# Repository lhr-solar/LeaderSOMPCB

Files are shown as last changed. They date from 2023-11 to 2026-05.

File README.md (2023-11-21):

# LeaderSOM
Author: Pratyush Patra and Jacob Pustilnik (and Tianda Huang)

This board is the Leader System-On-Module (SOM), a multifunction board with an STM32 MCU that is adaptible to the applications of each subsystem. The hardware and software on this board are responsible
for the processing, communication, and data collection tasks required for the car's subsystems.

## BOM
[**Interactive BOM (Must download and open in browser)**](bom/ibom.html)

[**Mouser Cart**]

## Connectors
| # | Name | Type | Ideal Voltage | Notes |
| - | - | - | - | - |

## PCB

## Schematic

## Additional Notes

## Current Board Concerns(8.26.2023)

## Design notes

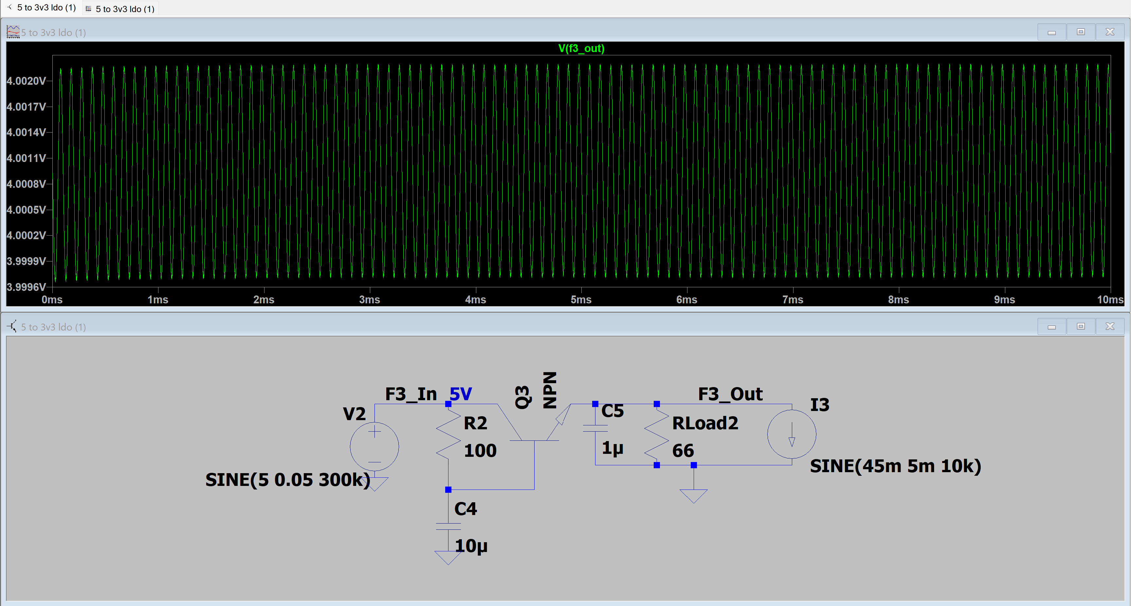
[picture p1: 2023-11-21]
PowerDistributionScreenshots/CapMultiplier.png

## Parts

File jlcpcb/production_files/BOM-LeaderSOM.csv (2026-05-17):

Comment | Designator | Footprint | LCSC | Quantity
0.1uF | C1,C11,C12,C19,C23,C24,C25,C26,C27,C28,C29,C30,C32,C35,C36,C37,C38,C39,C40,C41,C44,C5,C7,C8 | C_0603_1608Metric_Pad1.08x0.95mm_HandSolder | C14663 | 24
10k | R1,R12,R17,R22,R23,R29,R32,R33,R9 | R_0603_1608Metric_Pad0.98x0.95mm_HandSolder | C25804 | 9
10nF | C16 | C_0603_1608Metric_Pad1.08x0.95mm_HandSolder | C57112 | 1
10uF | C10,C13,C14,C20,C21,C22,C3,C42,C45 | C_0805_2012Metric_Pad1.18x1.45mm_HandSolder | C440198 | 9
120 | R10,R2 | R_0603_1608Metric_Pad0.98x0.95mm_HandSolder | C22787 | 2
16k | R15 | R_0603_1608Metric_Pad0.98x0.95mm_HandSolder | C137788 | 1
19k | R31 | R_0603_1608Metric_Pad0.98x0.95mm_HandSolder | C22893 | 1
1k | R19,R21,R28,R34,R35,R8 | R_0603_1608Metric_Pad0.98x0.95mm_HandSolder | C21190 | 6
1uF | C15,C18,C2,C43,C46,C9 | C_0603_1608Metric_Pad1.08x0.95mm_HandSolder | C15849 | 6
2.1k | R26 | R_0603_1608Metric_Pad0.98x0.95mm_HandSolder | C2960801 | 1
2.2k | R11,R3 | R_0603_1608Metric_Pad0.98x0.95mm_HandSolder | C4190 | 2
22.1k | R6 | R_0603_1608Metric_Pad0.98x0.95mm_HandSolder | C31850 | 1
24V | D4 | LED_0603_1608Metric_Pad1.05x0.95mm_HandSolder | C7371904 | 1
26p | C31,C33 | C_0603_1608Metric_Pad1.08x0.95mm_HandSolder | C92670 | 2
3.3nF | C17 | C_0603_1608Metric_Pad1.08x0.95mm_HandSolder | C107088 | 1
332 | R14 | R_0603_1608Metric_Pad0.98x0.95mm_HandSolder | C103549 | 1
3V3 | D21,D5 | LED_0603_1608Metric_Pad1.05x0.95mm_HandSolder | C7371904 | 2
4.3k | R18,R20 | R_0603_1608Metric_Pad0.98x0.95mm_HandSolder | C2907165 | 2
4.7uF | C34 | C_0805_2012Metric | C106218 | 1
4.7uF | C4,C6 | C_0805_2012Metric | C98192 | 2
402k | R27 | R_0603_1608Metric_Pad0.98x0.95mm_HandSolder | C2960796 | 1
45.3k | R24 | R_0603_1608Metric_Pad0.98x0.95mm_HandSolder | C2933224 | 1
47.5k | R7 | R_0603_1608Metric_Pad0.98x0.95mm_HandSolder | C25819 | 1
49.9 | R13 | R_0603_1608Metric_Pad0.98x0.95mm_HandSolder | C849792 | 1
5.1k | R4,R5 | R_0603_1608Metric_Pad0.98x0.95mm_HandSolder | C23186 | 2
590 | R25 | R_0603_1608Metric_Pad0.98x0.95mm_HandSolder | C23084 | 1
5V | D7 | LED_0603_1608Metric_Pad1.05x0.95mm_HandSolder | C7371904 | 1
74AHC1G32 | U8 | SOT-23-5 | C7470 | 1
8K | R30 | R_0603_1608Metric_Pad0.98x0.95mm_HandSolder | C2960681 | 1
8M | Y1 | Crystal_SMD_Abracon_ABM3-2Pin_5.0x3.2mm | C144380 | 1
BUCK | D20 | LED_0603_1608Metric_Pad1.05x0.95mm_HandSolder | C7371904 | 1
CDSOT23-T24CAN | U1,U3 | CDSOT23-T24CAN | C2959841 | 2
CP2102N-Axx-xQFN24 | U2 | CP2102N-A02-GQFN24 | C969151 | 1
D5V0P4UR6SO-7 | CR1,CR2,CR3 | D5V0P4UR6SO-7 | C531179 | 3
D_Schottky | D1,D18 | D_SOD-123 | C82544 | 2
D_TVS | D16 | D_SOD-323 | C207246 | 1
FerriteBead | FB1,FB2 | L_0603_1608Metric_Pad1.05x0.95mm_HandSolder | C14709 | 2
LED | CC_FLT1,IC_FLT1 | LED_0603_1608Metric_Pad1.05x0.95mm_HandSolder | C7371904 | 2
LM76202QPWPRQ1 | IC3 | LM76202QPWPRQ1 | C1849484 | 1
LT1963AEST-3.3#TRPBF | U4 | SOT-223-3_TabPin2 | C459918 | 1
MBR230S1F | D3 | D_SOD-123F | C151335 | 1
Micro_SD_Card_Det | J4 | microSD_HC_Hirose_DM3AT-SF-PEJM5 | C114218 | 1
PFLT | D6 | LED_0603_1608Metric_Pad1.05x0.95mm_HandSolder | C7371904 | 1
SD12_SOD323 | D17 | D_SOD-323 | C207246 | 1
SP0503BAHT | D2 | SOT-143 | C7074 | 1
STM32G473RETx | U7 | LQFP-64_10x10mm_P0.5mm | C730120 | 1
TCAN337DCNR | IC1,IC2 | TCAN337DCNR | C2671619 | 2
TPS2115ADRBR | U5 | SON65P300X300X100-9N | C140321 | 1
TPS5405DR | U6 | TPS5405DR | C488409 | 1
USB | D19 | LED_0603_1608Metric_Pad1.05x0.95mm_HandSolder | C7371904 | 1
USB_C_Receptacle_USB2.0_16P | J3 | USB_C_Receptacle_GCT_USB4105-xx-A_16P_TopMnt_Horizontal | C393939 | 1
WS2812B-2020 | D10,D11,D12,D13,D14,D15,D8,D9 | WS2812B-2020 | C965555 | 8
SWD | SWD1 | Molex_Nano-Fit_105309-xx04_1x04_P2.50mm_Vertical |  | 1
Reset | Reset1 | TL3365AF180QG |  | 1
100uH | L1 | L_Coilcraft_MSS1246-XXX |  | 1
SW_SPDT | SW1 | SW_CJS-1200TA |  | 1
52465-2470 | J1 | 524652470 |  | 1
52465-2470 | J2 | 524652470 |  | 1
TP_AddressableLED | TP1 | TestPoint_Pad_1.0x1.0mm |  | 1

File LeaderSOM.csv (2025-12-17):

Value | Qty | Mouser Part Number | DNP
0.1uF | 23 | MLASH168SB7104KTNA01
1uF | 6 | MLASU168SB5105KTNA01
10uF | 9 | GRM21BR61H106KE43K
4.7uF | 3 | 08055D475KAT4A
10nF | 1 | MSASH168SB5103KTNA01
3.3nF | 1 | 06035C332K4T2A
26p | 2 | 0603N270F500CT
100nF | 1 | MLASH168SB7104KTNA01
LED | 2 | 604-APTD2012LCGCK
D5V0P4UR6SO-7 | 3 | 621-D5V0P4UR6SO-7
D_Schottky | 1 | 1N5819HW-7-F
SP0503BAHT | 1 | 576-SP0503BAHTG
MBR230S1F | 1 | MP01EA06
24V | 1 | XL-1608UBC-06A
3V3 | 1 | XL-1608UBC-06A
PFLT | 1 | XL-1608UBC-06A
BUCK | 1 | XL-1608UBC-06A
WS2812B-2020 | 8 | WS2812-2020
D_TVS | 1 | 771-PESD15VL1BA-T/R
SD12_SOD323 | 1 | 771-PESD15VL1BA-T/R
TVS | 1 | MP01EA06
FerriteBead | 2 | 704-MFBW1V2012-121-R
TCAN337DCNR | 2 | 595-TCAN337DCNR
LM76202QPWPRQ1 | 1 | 595-LM76202QPWPRQ1
52465-2470 | 2 | 538-52465-2470
USB_C_Receptacle_USB2.0_16P | 1 | 640-USB4105-GF-A
Micro_SD_Card_Det | 1 | DM3AT-SF-PEJM5
100uH | 1 | MSS1246-104MLC
10k | 7 | CRCW060310K0FKEI
120 | 3 | CRCW0603120RFKEC
2.2k | 2 | CRCW06032K10FKEA
5.1k | 2 | CRCW06035K10FKEC
22.1k | 1 | CRCW060322K1FKEBC
47.5k | 1 | CRCW060347K5FKEAHP
1k | 1 | CRCW06031K00FKEI
49.9 | 1 | RT0603BRE0750RL
332 | 1 | CRCW0603332RFKEAHP
16k | 1 | CRCW060316K0FKEA
4.3k | 2 | CRCW06034K30FKTA
768 | 1 | CRCW0603768RFKEA
45.3k | 1 | CRCW060345K3FKEAHP
590 | 1 | CRCW0603590RFKEA
2.1k | 1 | CRCW06032K10FKEA
402k | 1 | CRCW0603402KFKEAC
10K | 1 | CRCW060310K0FKEI
8K | 1 | CRCW060310K0FKEI
19k | 1 | CRCW060320K0FKEA
Reset | 1 | 653-B3SL-1002P
SW_SPDT | 1 | CJS-1200TA
SWD | 1 | 105309-1104
CDSOT23-T24CAN | 2 | CDSOT23-T24CAN
CP2102N-Axx-xQFN24 | 1 | CP2102N-A02-GQFN24
LT1963AEST-3.3#TRPBF | 1 | LT1963AEST-3.3#TRPBF
TPS2115ADRBR | 1 | TPS2115ADRBR
TPS5405DR | 1 | TPS5405DR
STM32G473RETx | 1 | STM32G473RET6
74AHC1G32 | 1 | SN74AHC1G32TDBVRQ1
8M | 1 | ABM3-8.000MHZ-D2Y-T

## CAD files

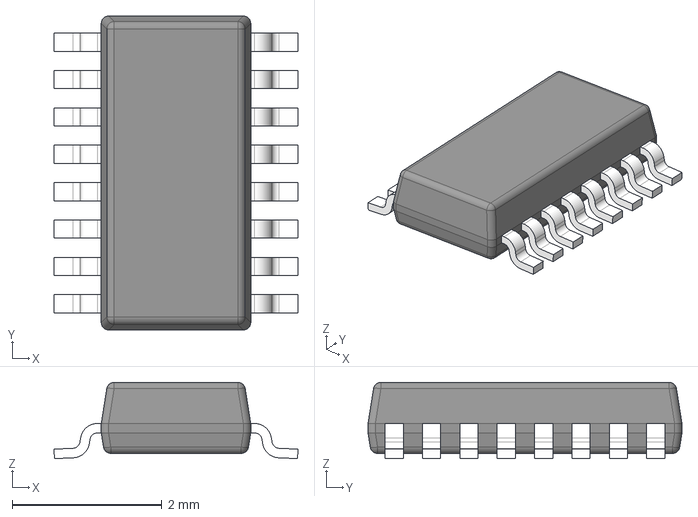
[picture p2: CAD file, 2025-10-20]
LSOM KiCad Libararies/SN74HCS595DYYR/DYY0016A.stp
3.26 x 4.20 x 1.02 mm
BODY-TSSOP
LEAD-TSSOP x 16

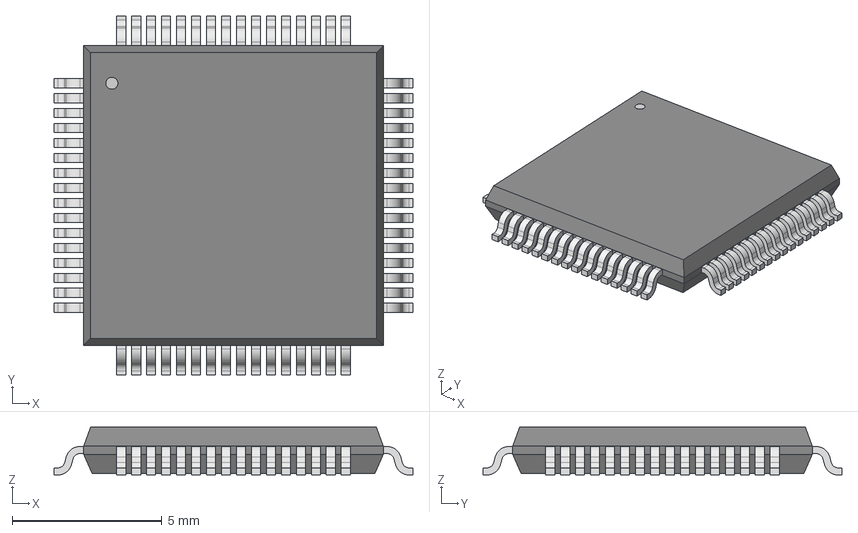
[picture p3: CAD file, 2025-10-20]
LSOM KiCad Libararies/STM32G473RET6/LQFP64-10x10mm.step
12.0 x 12.0 x 1.60 mm

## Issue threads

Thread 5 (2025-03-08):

Wrong Resistor Value for Power Protection

KadhirTheEngineer, 2025-03-08:
The 100k Pull up resistor for the UVLO pin on the Power Protection chip should be 10k resistor to get the right UVLO and OVLO values for the chip.

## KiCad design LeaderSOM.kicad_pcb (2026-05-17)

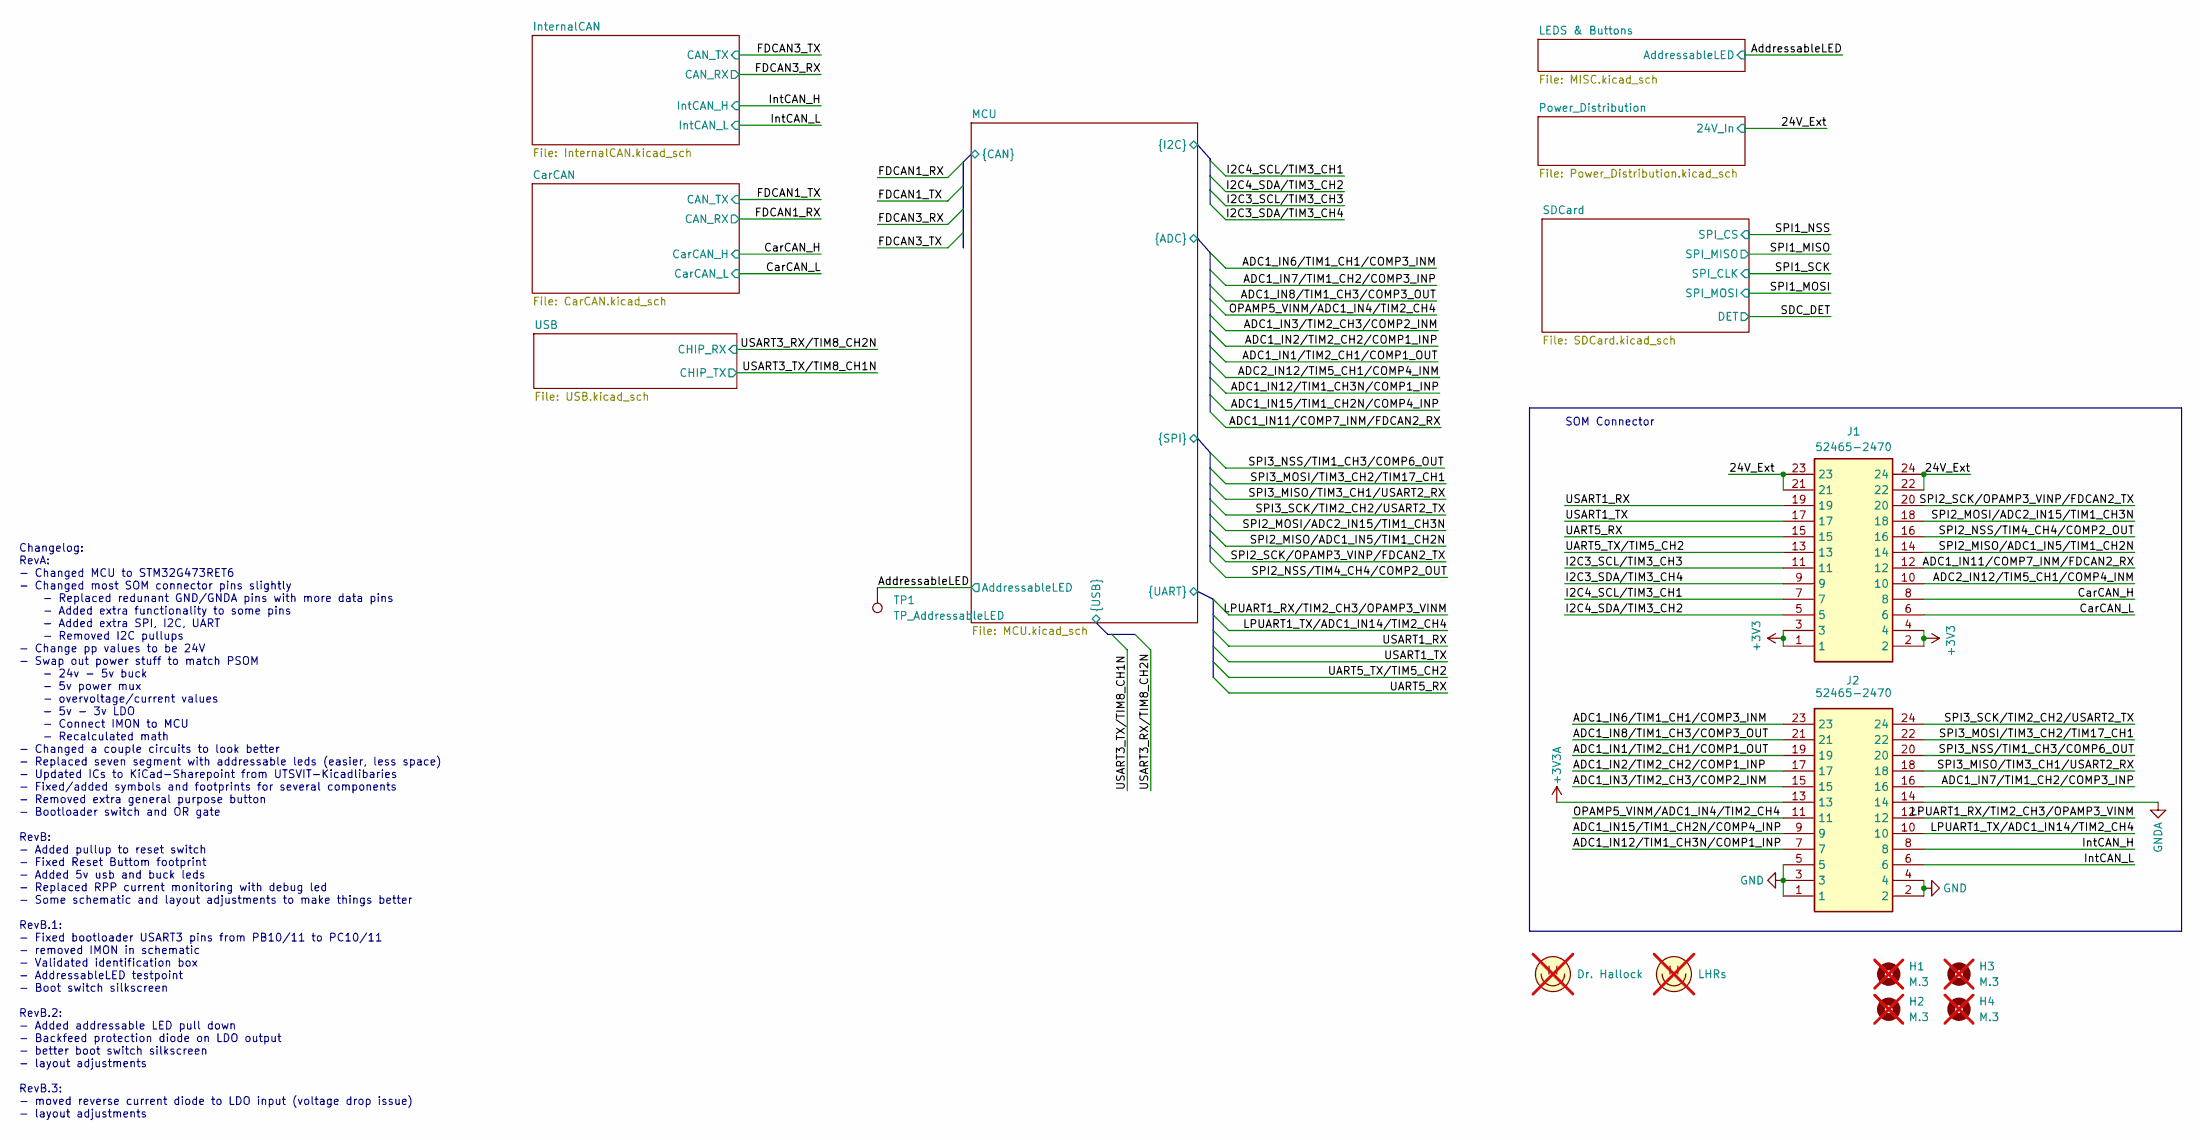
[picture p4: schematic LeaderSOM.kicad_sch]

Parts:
H1, H2, H3, H4: M.3; MountingHole_3.2mm_M3_Pad_TopBottom; not fitted
J1, J2: 52465-2470; 524652470; Mouser Part Number 538-52465-2470
LOGO1: Dr. Hallock; Hallock_Image_Tiny; not fitted
LOGO2: LHRs; LHRs_LOGO; not fitted
TP1: TP_AddressableLED; TestPoint_Pad_1.0x1.0mm

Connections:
+3V3: J1.1, J1.2, J1.3, J1.4; also elsewhere on the board
+3V3A: J2.13; also elsewhere on the board
/24V_Ext: J1.21, J1.22, J1.23, J1.24; also elsewhere on the board
/AddressableLED: TP1.1; also elsewhere on the board
/MCU/ADC1_IN1/TIM2_CH1/COMP1_OUT: J2.19; also elsewhere on the board
/MCU/ADC1_IN2/TIM2_CH2/COMP1_INP: J2.17; also elsewhere on the board
/MCU/ADC1_IN3/TIM2_CH3/COMP2_INM: J2.15; also elsewhere on the board
/MCU/ADC1_IN6/TIM1_CH1/COMP3_INM: J2.23; also elsewhere on the board
/MCU/ADC1_IN7/TIM1_CH2/COMP3_INP: J2.16; also elsewhere on the board
/MCU/ADC1_IN8/TIM1_CH3/COMP3_OUT: J2.21; also elsewhere on the board
/MCU/ADC1_IN11/COMP7_INM/FDCAN2_RX: J1.12; also elsewhere on the board
/MCU/ADC1_IN12/TIM1_CH3N/COMP1_INP: J2.7; also elsewhere on the board
/MCU/ADC1_IN15/TIM1_CH2N/COMP4_INP: J2.9; also elsewhere on the board
/MCU/ADC2_IN12/TIM5_CH1/COMP4_INM: J1.10; also elsewhere on the board
/MCU/CarCAN_H: J1.8; also elsewhere on the board
/MCU/CarCAN_L: J1.6; also elsewhere on the board
/MCU/I2C3_SCL/TIM3_CH3: J1.11; also elsewhere on the board
/MCU/I2C3_SDA/TIM3_CH4: J1.9; also elsewhere on the board
/MCU/I2C4_SCL/TIM3_CH1: J1.7; also elsewhere on the board
/MCU/I2C4_SDA/TIM3_CH2: J1.5; also elsewhere on the board
/MCU/IntCAN_H: J2.8; also elsewhere on the board
/MCU/IntCAN_L: J2.6; also elsewhere on the board
/MCU/LPUART1_RX/TIM2_CH3/OPAMP3_VINM: J2.12; also elsewhere on the board
/MCU/LPUART1_TX/ADC1_IN14/TIM2_CH4: J2.10; also elsewhere on the board
/MCU/OPAMP5_VINM/ADC1_IN4/TIM2_CH4: J2.11; also elsewhere on the board
/MCU/SPI2_MISO/ADC1_IN5/TIM1_CH2N: J1.14; also elsewhere on the board
/MCU/SPI2_MOSI/ADC2_IN15/TIM1_CH3N: J1.18; also elsewhere on the board
/MCU/SPI2_NSS/TIM4_CH4/COMP2_OUT: J1.16; also elsewhere on the board
/MCU/SPI2_SCK/OPAMP3_VINP/FDCAN2_TX: J1.20; also elsewhere on the board
/MCU/SPI3_MISO/TIM3_CH1/USART2_RX: J2.18; also elsewhere on the board
/MCU/SPI3_MOSI/TIM3_CH2/TIM17_CH1: J2.22; also elsewhere on the board
/MCU/SPI3_NSS/TIM1_CH3/COMP6_OUT: J2.20; also elsewhere on the board
/MCU/SPI3_SCK/TIM2_CH2/USART2_TX: J2.24; also elsewhere on the board
/MCU/UART5_RX: J1.15; also elsewhere on the board
/MCU/UART5_TX/TIM5_CH2: J1.13; also elsewhere on the board
/MCU/USART1_RX: J1.19; also elsewhere on the board
/MCU/USART1_TX: J1.17; also elsewhere on the board
GND: J2.1, J2.2, J2.3, J2.4, J2.5; also elsewhere on the board
GNDA: J2.14; also elsewhere on the board

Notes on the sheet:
Changelog: RevA: - Changed MCU to STM32G473RET6 - Changed most SOM connector pins slightly - Replaced redunant GND/GNDA pins with more data pins - Added extra functionality to some pins - Added extra SPI, I2C, UART - Removed I2C pullups - Change pp values to be 24V - Swap out power stuff to match P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
SOM Connector

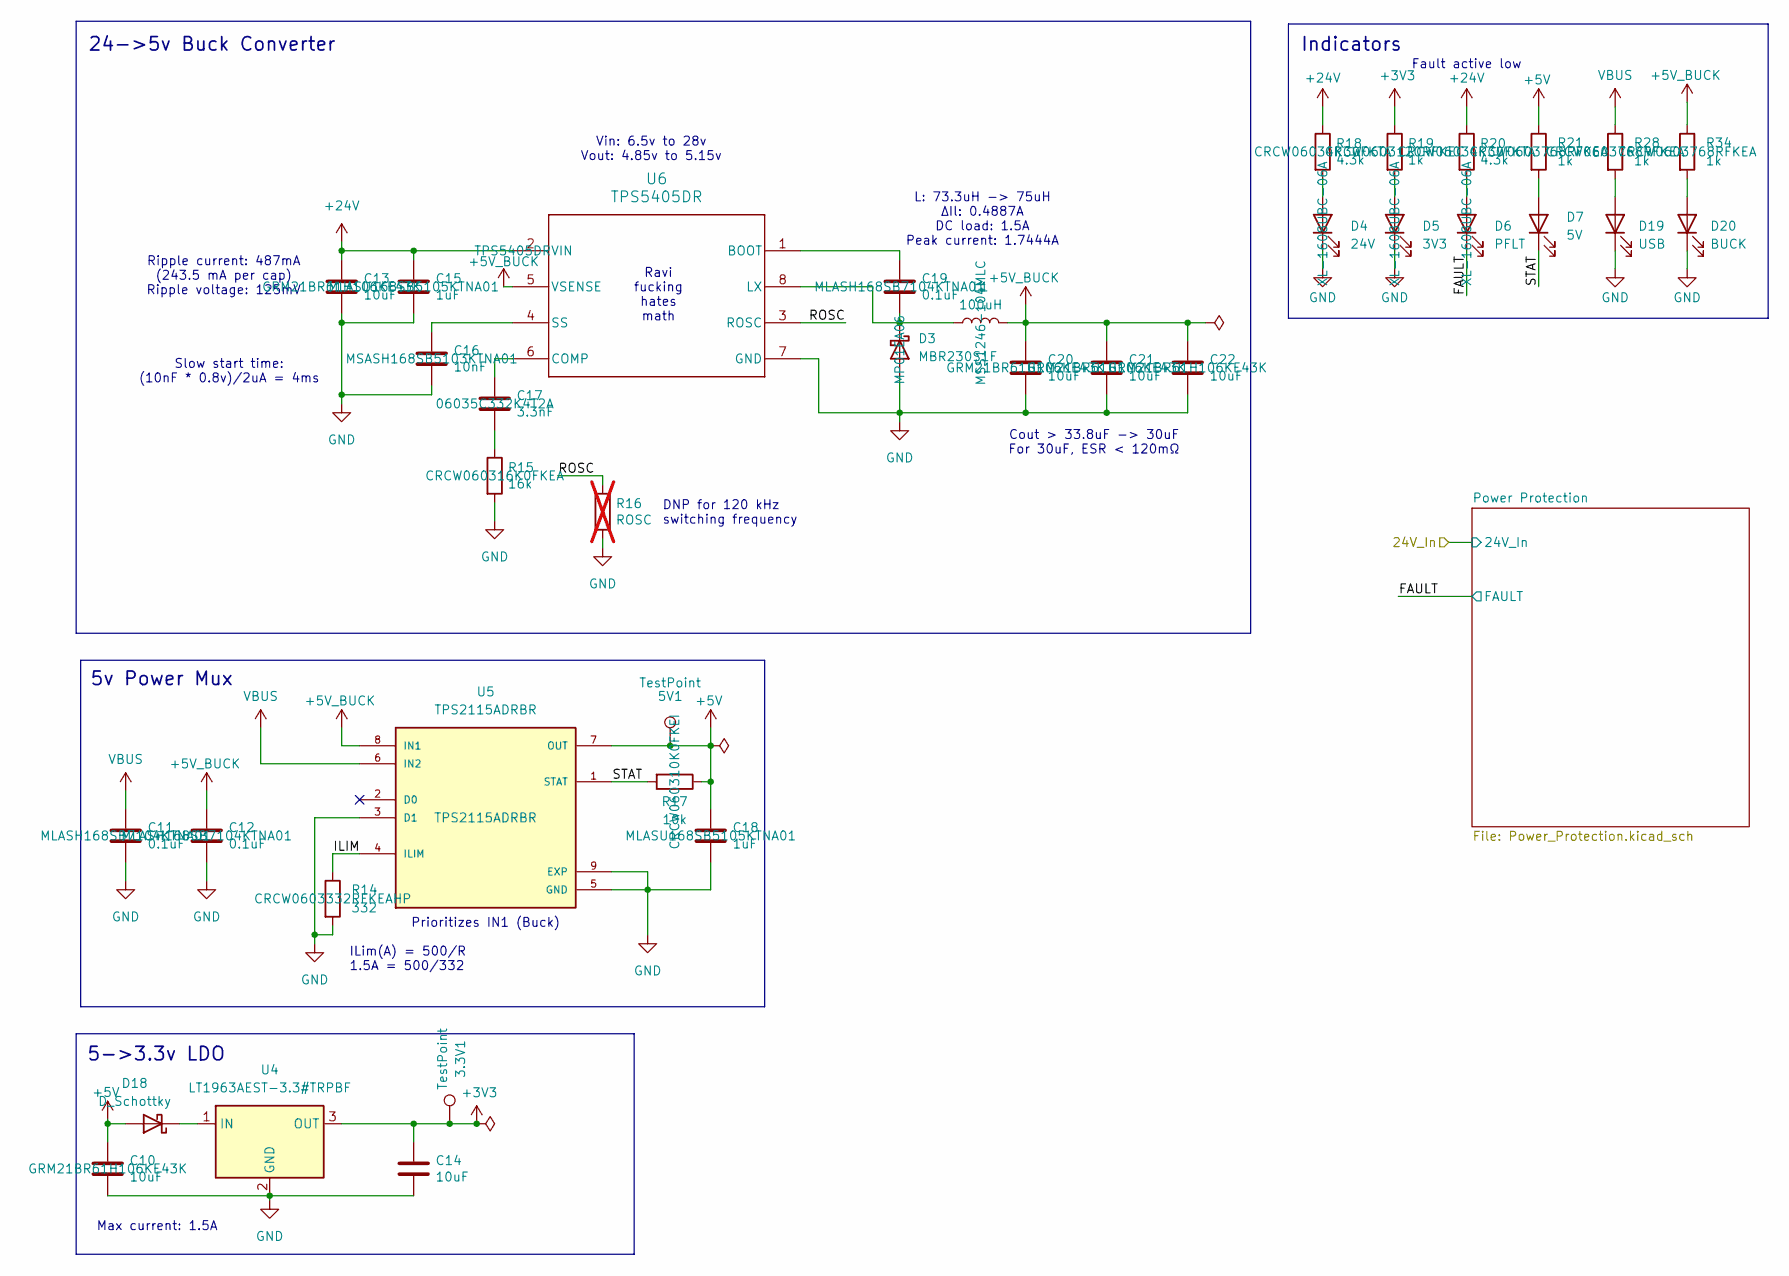
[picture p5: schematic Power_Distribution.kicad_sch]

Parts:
3.3V1, 5V1: TestPoint; TestPoint_Pad_1.0x1.0mm
C10, C13, C14, C20, C21, C22: 10uF; C_0805_2012Metric_Pad1.18x1.45mm_HandSolder; Mouser Part Number GRM21BR61H106KE43K
C11, C12, C19: 0.1uF; C_0603_1608Metric_Pad1.08x0.95mm_HandSolder; Mouser Part Number MLASH168SB7104KTNA01
C15, C18: 1uF; C_0603_1608Metric_Pad1.08x0.95mm_HandSolder; Mouser Part Number MLASU168SB5105KTNA01
C16: 10nF; C_0603_1608Metric_Pad1.08x0.95mm_HandSolder; Mouser Part Number MSASH168SB5103KTNA01
C17: 3.3nF; C_0603_1608Metric_Pad1.08x0.95mm_HandSolder; Mouser Part Number 06035C332K4T2A
D3: MBR230S1F; D_SOD-123F; Mouser Part Number MP01EA06
D4: 24V; LED_0603_1608Metric_Pad1.05x0.95mm_HandSolder; Mouser Part Number XL-1608UBC-06A
D5: 3V3; LED_0603_1608Metric_Pad1.05x0.95mm_HandSolder; Mouser Part Number XL-1608UBC-06A
D6: PFLT; LED_0603_1608Metric_Pad1.05x0.95mm_HandSolder; Mouser Part Number XL-1608UBC-06A
D7: 5V; LED_0603_1608Metric_Pad1.05x0.95mm_HandSolder; Mouser Part Number XL-1608UBC-06A
D18: D_Schottky; D_SOD-123; Mouser Part Number 1N5819HW-7-F
D19: USB; LED_0603_1608Metric_Pad1.05x0.95mm_HandSolder; Mouser Part Number XL-1608UBC-06A
D20: BUCK; LED_0603_1608Metric_Pad1.05x0.95mm_HandSolder; Mouser Part Number XL-1608UBC-06A
L1: 100uH; L_Coilcraft_MSS1246-XXX; Mouser Part Number MSS1246-104MLC
R14: 332; R_0603_1608Metric_Pad0.98x0.95mm_HandSolder; Mouser Part Number CRCW0603332RFKEAHP
R15: 16k; R_0603_1608Metric_Pad0.98x0.95mm_HandSolder; Mouser Part Number CRCW060316K0FKEA
R16: ROSC; R_0603_1608Metric_Pad0.98x0.95mm_HandSolder; not fitted
R17: 10k; R_0603_1608Metric_Pad0.98x0.95mm_HandSolder; Mouser Part Number CRCW060310K0FKEI
R18, R20: 4.3k; R_0603_1608Metric_Pad0.98x0.95mm_HandSolder; Mouser Part Number CRCW06034K30FKTA
R19: 1k; R_0603_1608Metric_Pad0.98x0.95mm_HandSolder; Mouser Part Number CRCW0603120RFKEC
R21, R28, R34: 1k; R_0603_1608Metric_Pad0.98x0.95mm_HandSolder; Mouser Part Number CRCW0603768RFKEA
U4: LT1963AEST-3.3#TRPBF; SOT-223-3_TabPin2; Mouser Part Number LT1963AEST-3.3#TRPBF
U5: TPS2115ADRBR; SON65P300X300X100-9N; Mouser Part Number TPS2115ADRBR
U6: TPS5405DR; Mouser Part Number TPS5405DR

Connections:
+3V3: 3.3V1.1, C14.1, R19.1, U4.3 (OUT); also elsewhere on the board
+5V: 5V1.1, C10.1, C18.1, D18.2 (A), R17.1, R21.1, U5.7 (OUT); also elsewhere on the board
+5V_BUCK: C12.1, C20.1, C21.1, C22.1, L1.2, R34.1, U5.8 (IN1), U6.5 (VSENSE)
+24V: C13.1, C15.1, R18.1, R20.1, U6.2 (VIN); also elsewhere on the board
/Power_Distribution/FAULT: D6.1 (K); also elsewhere on the board
/Power_Distribution/ILIM: R14.1, U5.4 (ILIM)
/Power_Distribution/ROSC: R16.1, U6.3 (ROSC)
/Power_Distribution/STAT: D7.1 (K), R17.2, U5.1 (STAT)
GND: C10.2, C11.2, C12.2, C13.2, C14.2, C15.2, C16.2, C18.2, C20.2, C21.2, C22.2, D3.2 (A), D4.1 (K), D5.1 (K), D19.1 (K), D20.1 (K), R14.2, R15.2, R16.2, U4.2 (GND), U5.3 (D1), U5.5 (GND), U5.9 (EXP), U6.7 (GND); also elsewhere on the board
unnamed: C17.2, R15.1
unnamed: C19.2, D3.1 (K), L1.1, U6.8 (LX)
unnamed: D4.2 (A), R18.2
unnamed: D5.2 (A), R19.2
unnamed: D6.2 (A), R20.2
unnamed: D7.2 (A), R21.2
unnamed: D18.1 (K), U4.1 (IN)
unnamed: D19.2 (A), R28.2
unnamed: D20.2 (A), R34.2
unnamed: C19.1, U6.1 (BOOT)
unnamed: C17.1, U6.6 (COMP)
unnamed: C16.1, U6.4 (SS)
VBUS: C11.1, R28.1, U5.6 (IN2); also elsewhere on the board

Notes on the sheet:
Max current: 1.5A
Vin: 6.5v to 28v Vout: 4.85v to 5.15v
DNP for 120 kHz switching frequency
Ravi fucking hates math
Indicators
Prioritizes IN1 (Buck)
Cout > 33.8uF -> 30uF For 30uF, ESR < 120mΩ
Fault active low
ILim(A) = 500/R 1.5A = 500/332
Slow start time: (10nF * 0.8v)/2uA = 4ms
5->3.3v LDO
24->5v Buck Converter
5v Power Mux
Ripple current: 487mA (243.5 mA per cap) Ripple voltage: 125mV
L: 73.3uH -> 75uH ΔIl: 0.4887A DC load: 1.5A Peak current: 1.7444A

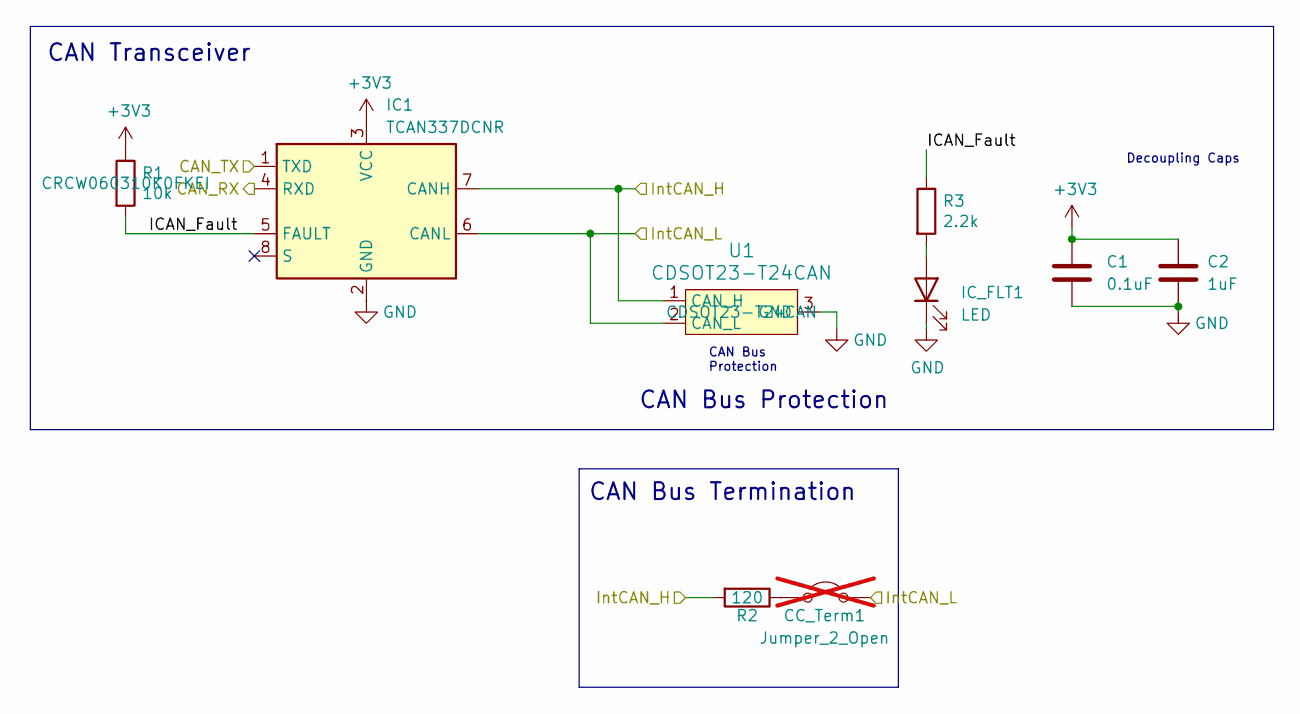
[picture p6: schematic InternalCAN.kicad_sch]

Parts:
C1: 0.1uF; C_0603_1608Metric_Pad1.08x0.95mm_HandSolder; Mouser Part Number MLASH168SB7104KTNA01
C2: 1uF; C_0603_1608Metric_Pad1.08x0.95mm_HandSolder; Mouser Part Number MLASU168SB5105KTNA01
CC_Term1: Jumper_2_Open; PinHeader_1x02_P2.54mm_Vertical; not fitted
IC1: TCAN337DCNR; Mouser Part Number 595-TCAN337DCNR
IC_FLT1: LED; LED_0603_1608Metric_Pad1.05x0.95mm_HandSolder; Mouser Part Number 604-APTD2012LCGCK
R1: 10k; R_0603_1608Metric_Pad0.98x0.95mm_HandSolder; Mouser Part Number CRCW060310K0FKEI
R2: 120; R_0603_1608Metric_Pad0.98x0.95mm_HandSolder; Mouser Part Number CRCW0603120RFKEC
R3: 2.2k; R_0603_1608Metric_Pad0.98x0.95mm_HandSolder; Mouser Part Number CRCW06032K10FKEA
U1: CDSOT23-T24CAN; Mouser Part Number CDSOT23-T24CAN

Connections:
+3V3: C1.1, C2.1, IC1.3 (VCC), R1.1; also elsewhere on the board
/InternalCAN/ICAN_Fault: IC1.5 (FAULT), R1.2, R3.1
/MCU/FDCAN3_RX: IC1.4 (RXD); also elsewhere on the board
/MCU/FDCAN3_TX: IC1.1 (TXD); also elsewhere on the board
/MCU/IntCAN_H: IC1.7 (CANH), R2.2, U1.1 (CAN_H); also elsewhere on the board
/MCU/IntCAN_L: CC_Term1.2 (B), IC1.6 (CANL), U1.2 (CAN_L); also elsewhere on the board
GND: C1.2, C2.2, IC1.2 (GND), IC_FLT1.1 (K), U1.3 (GND); also elsewhere on the board
unnamed: CC_Term1.1 (A), R2.1
unnamed: IC_FLT1.2 (A), R3.2

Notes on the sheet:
CAN Bus Protection
CAN Bus Termination
CAN Transceiver
CAN Bus Protection
Decoupling Caps

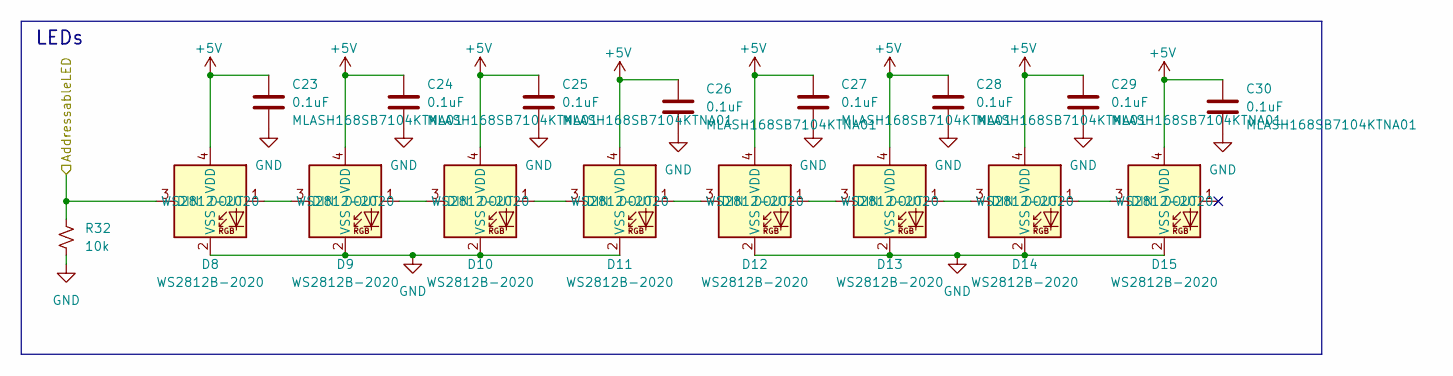
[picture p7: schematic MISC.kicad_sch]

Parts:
C23, C24, C25, C26, C27, C28, C29, C30: 0.1uF; C_0603_1608Metric_Pad1.08x0.95mm_HandSolder; Mouser Part Number MLASH168SB7104KTNA01
D8, D9, D10, D11, D12, D13, D14, D15: WS2812B-2020; Mouser Part Number WS2812-2020
R32: 10k; R_0603_1608Metric_Pad0.98x0.95mm_HandSolder

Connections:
+5V: C23.1, C24.1, C25.1, C26.1, C27.1, C28.1, C29.1, C30.1, D8.4 (VDD), D9.4 (VDD), D10.4 (VDD), D11.4 (VDD), D12.4 (VDD), D13.4 (VDD), D14.4 (VDD), D15.4 (VDD); also elsewhere on the board
/AddressableLED: D8.3 (DIN), R32.1; also elsewhere on the board
GND: C23.2, C24.2, C25.2, C26.2, C27.2, C28.2, C29.2, C30.2, D8.2 (VSS), D9.2 (VSS), D10.2 (VSS), D11.2 (VSS), D12.2 (VSS), D13.2 (VSS), D14.2 (VSS), D15.2 (VSS), R32.2; also elsewhere on the board
unnamed: D8.1 (DOUT), D9.3 (DIN)
unnamed: D9.1 (DOUT), D10.3 (DIN)
unnamed: D10.1 (DOUT), D11.3 (DIN)
unnamed: D11.1 (DOUT), D12.3 (DIN)
unnamed: D12.1 (DOUT), D13.3 (DIN)
unnamed: D13.1 (DOUT), D14.3 (DIN)
unnamed: D14.1 (DOUT), D15.3 (DIN)

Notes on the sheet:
LEDs

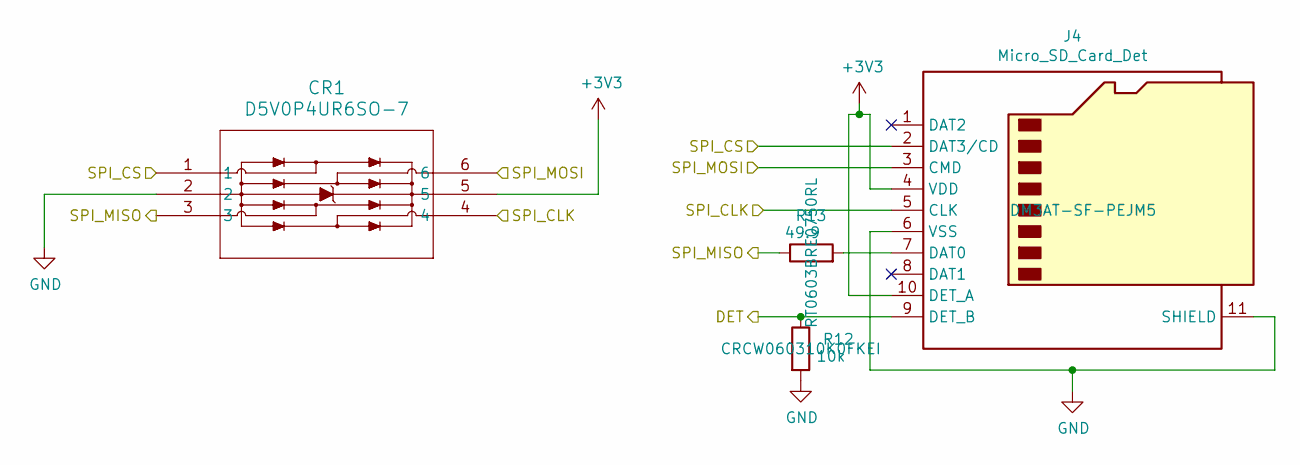
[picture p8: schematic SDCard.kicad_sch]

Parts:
CR1: D5V0P4UR6SO-7; Mouser Part Number 621-D5V0P4UR6SO-7
J4: Micro_SD_Card_Det; microSD_HC_Hirose_DM3AT-SF-PEJM5; Mouser Part Number DM3AT-SF-PEJM5
R12: 10k; R_0603_1608Metric_Pad0.98x0.95mm_HandSolder; Mouser Part Number CRCW060310K0FKEI
R13: 49.9; R_0603_1608Metric_Pad0.98x0.95mm_HandSolder; Mouser Part Number RT0603BRE0750RL

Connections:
+3V3: CR1.5, J4.4 (VDD), J4.10 (DET_A); also elsewhere on the board
/MCU/SDC_DET: J4.9 (DET_B), R12.1; also elsewhere on the board
/MCU/SPI1_MISO: CR1.3, R13.1; also elsewhere on the board
/MCU/SPI1_MOSI: CR1.6, J4.3 (CMD); also elsewhere on the board
/MCU/SPI1_NSS: CR1.1, J4.2 (DAT3/CD); also elsewhere on the board
/MCU/SPI1_SCK: CR1.4, J4.5 (CLK); also elsewhere on the board
GND: CR1.2, J4.6 (VSS), J4.11 (SHIELD), R12.2; also elsewhere on the board
unnamed: J4.7 (DAT0), R13.2

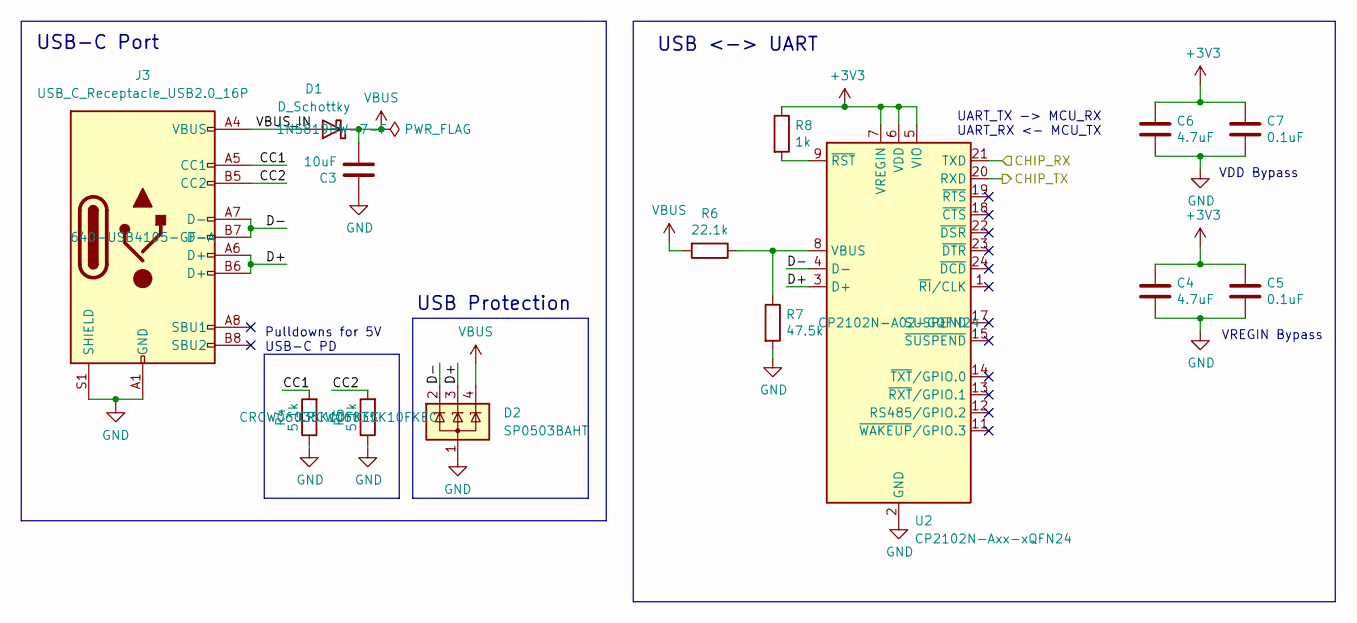
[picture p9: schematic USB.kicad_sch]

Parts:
C3: 10uF; C_0805_2012Metric; Mouser Part Number GRM21BR61H106KE43K
C4, C6: 4.7uF; C_0805_2012Metric; Mouser Part Number 08055D475KAT4A
C5, C7: 0.1uF; C_0603_1608Metric_Pad1.08x0.95mm_HandSolder; Mouser Part Number MLASH168SB7104KTNA01
D1: D_Schottky; D_SOD-123; Mouser Part Number 1N5819HW-7-F
D2: SP0503BAHT; SOT-143; Mouser Part Number 576-SP0503BAHTG
J3: USB_C_Receptacle_USB2.0_16P; USB_C_Receptacle_GCT_USB4105-xx-A_16P_TopMnt_Horizontal; Mouser Part Number 640-USB4105-GF-A
R4, R5: 5.1k; R_0603_1608Metric_Pad0.98x0.95mm_HandSolder; Mouser Part Number CRCW06035K10FKEC
R6: 22.1k; R_0603_1608Metric_Pad0.98x0.95mm_HandSolder; Mouser Part Number CRCW060322K1FKEBC
R7: 47.5k; R_0603_1608Metric_Pad0.98x0.95mm_HandSolder; Mouser Part Number CRCW060347K5FKEAHP
R8: 1k; R_0603_1608Metric_Pad0.98x0.95mm_HandSolder; Mouser Part Number CRCW06031K00FKEI
U2: CP2102N-Axx-xQFN24; CP2102N-A02-GQFN24; Mouser Part Number CP2102N-A02-GQFN24

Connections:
+3V3: C4.1, C5.1, C6.1, C7.1, R8.1, U2.5 (VIO), U2.6 (VDD), U2.7 (VREGIN); also elsewhere on the board
/MCU/USART3_RX/TIM8_CH2N: U2.21 (TXD); also elsewhere on the board
/MCU/USART3_TX/TIM8_CH1N: U2.20 (RXD); also elsewhere on the board
/USB/CC1: J3.A5 (CC1), R4.2
/USB/CC2: J3.B5 (CC2), R5.2
/USB/D+: D2.3 (K), J3.A6 (D+), J3.B6 (D+), U2.3 (D+)
/USB/D-: D2.2 (K), J3.A7 (D-), J3.B7 (D-), U2.4 (D-)
/USB/VBUS_IN: D1.2 (A), J3.A4 (VBUS), J3.A9 (VBUS), J3.B4 (VBUS), J3.B9 (VBUS)
GND: C3.1, C4.2, C5.2, C6.2, C7.2, D2.1 (A), J3.A1 (GND), J3.A12 (GND), J3.B1 (GND), J3.B12 (GND), J3.S1 (SHIELD), J3.S2 (Shield), J3.S3 (Shield), J3.S4 (Shield), R4.1, R5.1, R7.2, U2.2 (GND), U2.25 (GND); also elsewhere on the board
unnamed: R6.1, R7.1, U2.8 (VBUS)
unnamed: R8.2, U2.9 (~RST)
VBUS: C3.2, D1.1 (K), D2.4 (K), R6.2; also elsewhere on the board

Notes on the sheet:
VDD Bypass
USB Protection
USB-C Port
VREGIN Bypass
Pulldowns for 5V USB-C PD
USB <-> UART
UART_TX -> MCU_RX UART_RX <- MCU_TX

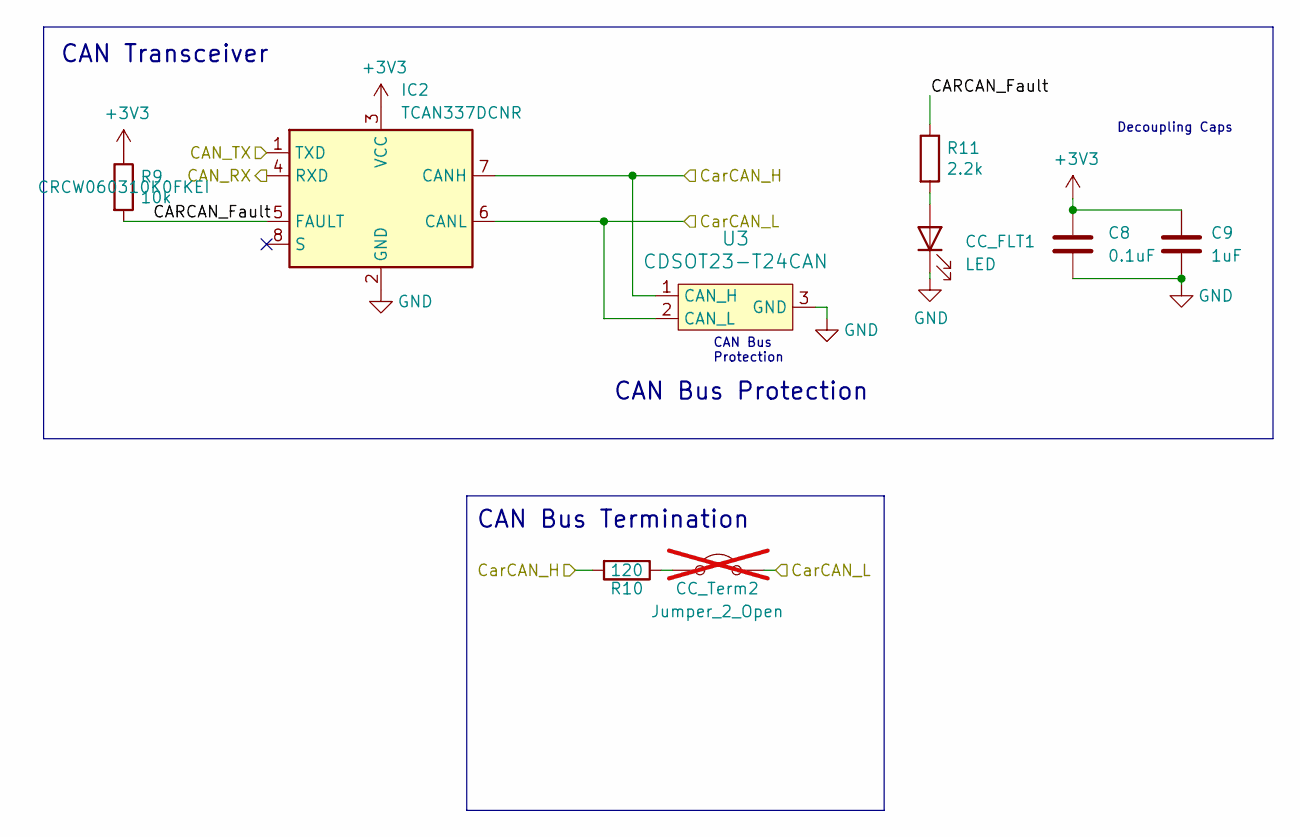
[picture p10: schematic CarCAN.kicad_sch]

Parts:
C8: 0.1uF; C_0603_1608Metric_Pad1.08x0.95mm_HandSolder; Mouser Part Number MLASH168SB7104KTNA01
C9: 1uF; C_0603_1608Metric_Pad1.08x0.95mm_HandSolder; Mouser Part Number MLASU168SB5105KTNA01
CC_FLT1: LED; LED_0603_1608Metric_Pad1.05x0.95mm_HandSolder; Mouser Part Number 604-APTD2012LCGCK
CC_Term2: Jumper_2_Open; PinHeader_1x02_P2.54mm_Vertical; not fitted
IC2: TCAN337DCNR; Mouser Part Number 595-TCAN337DCNR
R9: 10k; R_0603_1608Metric_Pad0.98x0.95mm_HandSolder; Mouser Part Number CRCW060310K0FKEI
R10: 120; R_0603_1608Metric_Pad0.98x0.95mm_HandSolder; Mouser Part Number CRCW0603120RFKEC
R11: 2.2k; R_0603_1608Metric_Pad0.98x0.95mm_HandSolder; Mouser Part Number CRCW06032K10FKEA
U3: CDSOT23-T24CAN; Mouser Part Number CDSOT23-T24CAN

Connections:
+3V3: C8.1, C9.1, IC2.3 (VCC), R9.1; also elsewhere on the board
/CarCAN/CARCAN_Fault: IC2.5 (FAULT), R9.2, R11.1
/MCU/CarCAN_H: IC2.7 (CANH), R10.2, U3.1 (CAN_H); also elsewhere on the board
/MCU/CarCAN_L: CC_Term2.2 (B), IC2.6 (CANL), U3.2 (CAN_L); also elsewhere on the board
/MCU/FDCAN1_RX: IC2.4 (RXD); also elsewhere on the board
/MCU/FDCAN1_TX: IC2.1 (TXD); also elsewhere on the board
GND: C8.2, C9.2, CC_FLT1.1 (K), IC2.2 (GND), U3.3 (GND); also elsewhere on the board
unnamed: CC_FLT1.2 (A), R11.2
unnamed: CC_Term2.1 (A), R10.1

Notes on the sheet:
CAN Bus Protection
CAN Bus Termination
CAN Bus Protection
CAN Transceiver
Decoupling Caps

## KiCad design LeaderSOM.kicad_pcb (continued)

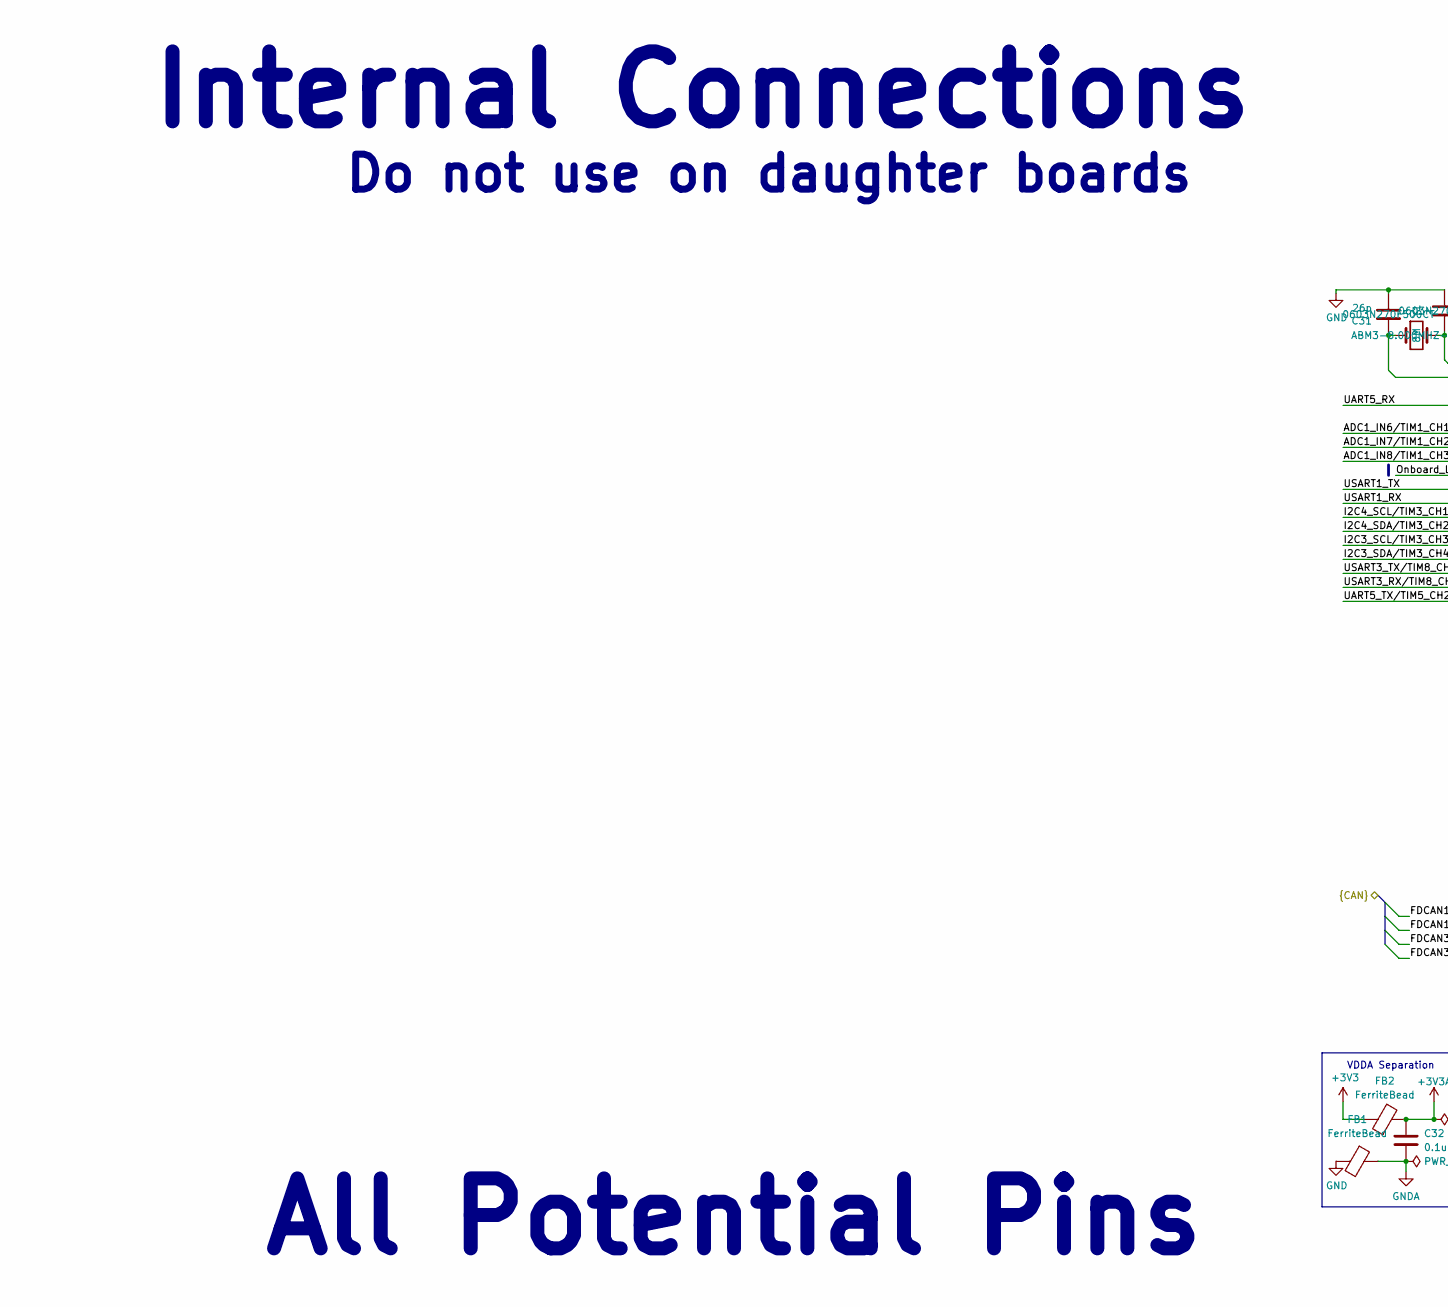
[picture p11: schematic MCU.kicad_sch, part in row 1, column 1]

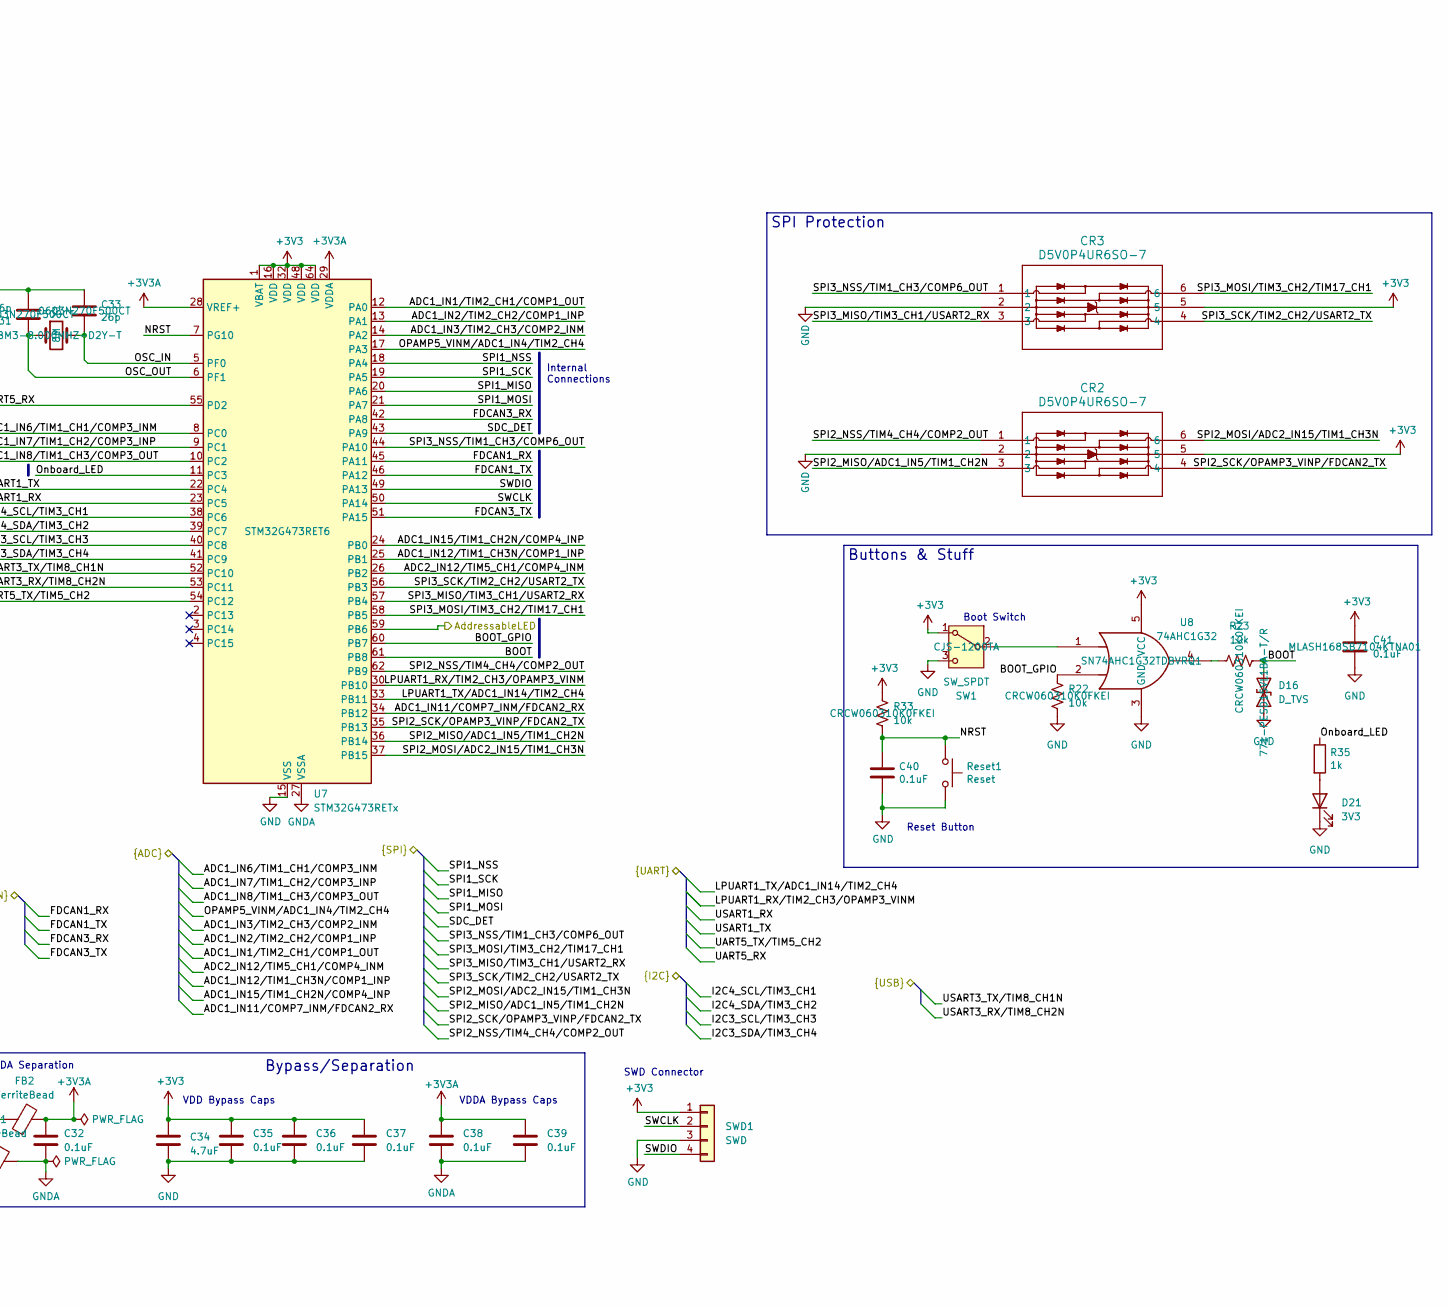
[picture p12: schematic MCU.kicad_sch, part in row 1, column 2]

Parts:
C31, C33: 26p; C_0603_1608Metric_Pad1.08x0.95mm_HandSolder; Mouser Part Number 0603N270F500CT
C32, C35, C36, C37, C38, C39, C40, C41: 0.1uF; C_0603_1608Metric_Pad1.08x0.95mm_HandSolder; Mouser Part Number MLASH168SB7104KTNA01
C34: 4.7uF; C_0805_2012Metric; Mouser Part Number 08055D475KAT4A
CR2, CR3: D5V0P4UR6SO-7; Mouser Part Number 621-D5V0P4UR6SO-7
D16: D_TVS; D_SOD-323; Mouser Part Number 771-PESD15VL1BA-T/R
D21: 3V3; LED_0603_1608Metric_Pad1.05x0.95mm_HandSolder; Mouser Part Number XL-1608UBC-06A
FB1, FB2: FerriteBead; L_0603_1608Metric_Pad1.05x0.95mm_HandSolder; Mouser Part Number 704-MFBW1V2012-121-R
R22, R23, R33: 10k; R_0603_1608Metric_Pad0.98x0.95mm_HandSolder; Mouser Part Number CRCW060310K0FKEI
R35: 1k; R_0603_1608Metric_Pad0.98x0.95mm_HandSolder; Mouser Part Number CRCW0603120RFKEC
Reset1: Reset; TL3365AF180QG; Mouser Part Number 612-TL3365AF180QG
SW1: SW_SPDT; SW_CJS-1200TA; Mouser Part Number CJS-1200TA
SWD1: SWD; Molex_Nano-Fit_105309-xx04_1x04_P2.50mm_Vertical; Mouser Part Number 105309-1104
U7: STM32G473RETx; LQFP-64_10x10mm_P0.5mm; Mouser Part Number STM32G473RET6
U8: 74AHC1G32; SOT-23-5; Mouser Part Number SN74AHC1G32TDBVRQ1
Y1: 8M; Crystal_SMD_Abracon_ABM3-2Pin_5.0x3.2mm; Mouser Part Number ABM3-8.000MHZ-D2Y-T

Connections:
+3V3: C34.1, C35.1, C36.1, C37.1, C41.1, CR2.5, CR3.5, FB2.1, R33.2, SW1.1 (A), SWD1.1, U7.1 (VBAT), U7.16 (VDD), U7.32 (VDD), U7.48 (VDD), U7.64 (VDD), U8.5 (VCC); also elsewhere on the board
+3V3A: C32.1, C38.1, C39.1, FB2.2, U7.28 (VREF+), U7.29 (VDDA); also elsewhere on the board
/AddressableLED: U7.59 (PB6); also elsewhere on the board
/MCU/ADC1_IN1/TIM2_CH1/COMP1_OUT: U7.12 (PA0); also elsewhere on the board
/MCU/ADC1_IN2/TIM2_CH2/COMP1_INP: U7.13 (PA1); also elsewhere on the board
/MCU/ADC1_IN3/TIM2_CH3/COMP2_INM: U7.14 (PA2); also elsewhere on the board
/MCU/ADC1_IN6/TIM1_CH1/COMP3_INM: U7.8 (PC0); also elsewhere on the board
/MCU/ADC1_IN7/TIM1_CH2/COMP3_INP: U7.9 (PC1); also elsewhere on the board
/MCU/ADC1_IN8/TIM1_CH3/COMP3_OUT: U7.10 (PC2); also elsewhere on the board
/MCU/ADC1_IN11/COMP7_INM/FDCAN2_RX: U7.34 (PB12); also elsewhere on the board
/MCU/ADC1_IN12/TIM1_CH3N/COMP1_INP: U7.25 (PB1); also elsewhere on the board
/MCU/ADC1_IN15/TIM1_CH2N/COMP4_INP: U7.24 (PB0); also elsewhere on the board
/MCU/ADC2_IN12/TIM5_CH1/COMP4_INM: U7.26 (PB2); also elsewhere on the board
/MCU/BOOT: D16.2 (A2), R23.2, U7.61 (PB8)
/MCU/BOOT_GPIO: R22.2, U7.60 (PB7), U8.2
/MCU/FDCAN1_RX: U7.45 (PA11); also elsewhere on the board
/MCU/FDCAN1_TX: U7.46 (PA12); also elsewhere on the board
/MCU/FDCAN3_RX: U7.42 (PA8); also elsewhere on the board
/MCU/FDCAN3_TX: U7.51 (PA15); also elsewhere on the board
/MCU/I2C3_SCL/TIM3_CH3: U7.40 (PC8); also elsewhere on the board
/MCU/I2C3_SDA/TIM3_CH4: U7.41 (PC9); also elsewhere on the board
/MCU/I2C4_SCL/TIM3_CH1: U7.38 (PC6); also elsewhere on the board
/MCU/I2C4_SDA/TIM3_CH2: U7.39 (PC7); also elsewhere on the board
/MCU/LPUART1_RX/TIM2_CH3/OPAMP3_VINM: U7.30 (PB10); also elsewhere on the board
/MCU/LPUART1_TX/ADC1_IN14/TIM2_CH4: U7.33 (PB11); also elsewhere on the board
/MCU/NRST: C40.1, R33.1, Reset1.1, U7.7 (PG10)
/MCU/OPAMP5_VINM/ADC1_IN4/TIM2_CH4: U7.17 (PA3); also elsewhere on the board
/MCU/OSC_IN: C33.2, U7.5 (PF0), Y1.2
/MCU/OSC_OUT: C31.1, U7.6 (PF1), Y1.1
/MCU/Onboard_LED: R35.1, U7.11 (PC3)
/MCU/SDC_DET: U7.43 (PA9); also elsewhere on the board
/MCU/SPI1_MISO: U7.20 (PA6); also elsewhere on the board
/MCU/SPI1_MOSI: U7.21 (PA7); also elsewhere on the board
/MCU/SPI1_NSS: U7.18 (PA4); also elsewhere on the board
/MCU/SPI1_SCK: U7.19 (PA5); also elsewhere on the board
/MCU/SPI2_MISO/ADC1_IN5/TIM1_CH2N: CR2.3, U7.36 (PB14); also elsewhere on the board
/MCU/SPI2_MOSI/ADC2_IN15/TIM1_CH3N: CR2.6, U7.37 (PB15); also elsewhere on the board
/MCU/SPI2_NSS/TIM4_CH4/COMP2_OUT: CR2.1, U7.62 (PB9); also elsewhere on the board
/MCU/SPI2_SCK/OPAMP3_VINP/FDCAN2_TX: CR2.4, U7.35 (PB13); also elsewhere on the board
/MCU/SPI3_MISO/TIM3_CH1/USART2_RX: CR3.3, U7.57 (PB4); also elsewhere on the board
/MCU/SPI3_MOSI/TIM3_CH2/TIM17_CH1: CR3.6, U7.58 (PB5); also elsewhere on the board
/MCU/SPI3_NSS/TIM1_CH3/COMP6_OUT: CR3.1, U7.44 (PA10); also elsewhere on the board
/MCU/SPI3_SCK/TIM2_CH2/USART2_TX: CR3.4, U7.56 (PB3); also elsewhere on the board
/MCU/SWCLK: SWD1.2, U7.50 (PA14)
/MCU/SWDIO: SWD1.4, U7.49 (PA13)
/MCU/UART5_RX: U7.55 (PD2); also elsewhere on the board
/MCU/UART5_TX/TIM5_CH2: U7.54 (PC12); also elsewhere on the board
/MCU/USART1_RX: U7.23 (PC5); also elsewhere on the board
/MCU/USART1_TX: U7.22 (PC4); also elsewhere on the board
/MCU/USART3_RX/TIM8_CH2N: U7.53 (PC11); also elsewhere on the board
/MCU/USART3_TX/TIM8_CH1N: U7.52 (PC10); also elsewhere on the board
GND: C31.2, C33.1, C34.2, C35.2, C36.2, C37.2, C40.2, C41.2, CR2.2, CR3.2, D16.1 (A1), D21.1 (K), FB1.2, R22.1, Reset1.2, SW1.3 (C), SWD1.3, U7.15 (VSS), U7.31 (VSS), U7.47 (VSS), U7.63 (VSS), U8.3 (GND); also elsewhere on the board
GNDA: C32.2, C38.2, C39.2, FB1.1, U7.27 (VSSA); also elsewhere on the board
unnamed: D21.2 (A), R35.2
unnamed: R23.1, U8.4
unnamed: SW1.2 (B), U8.1

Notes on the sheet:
Do not use on daughter boards
Internal Connections
Boot Switch
VDDA Bypass Caps
Bypass/Separation
Reset Button
SWD Connector
SPI Protection
VDD Bypass Caps
All Potential Pins
Internal Connections
VDDA Separation
Buttons & Stuff

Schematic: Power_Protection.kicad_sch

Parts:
24V2: TestPoint; TestPoint_Pad_1.0x1.0mm
C42, C45: 10uF; C_0805_2012Metric; Mouser Part Number GRM21BR61H106KE43K
C43, C46: 1uF; C_0603_1608Metric_Pad1.08x0.95mm_HandSolder; Mouser Part Number MLASU168SB5105KTNA01
C44: 0.1uF; C_0603_1608Metric_Pad1.08x0.95mm_HandSolder; Mouser Part Number MLASH168SB7104KTNA01
D17: SD12_SOD323; D_SOD-323; Mouser Part Number 771-PESD15VL1BA-T/R
GND1: TestPoint; TestPoint_Pad_1.0x1.0mm
IC3: LM76202QPWPRQ1; Mouser Part Number 595-LM76202QPWPRQ1
R24: 45.3k; R_0603_1608Metric_Pad0.98x0.95mm_HandSolder; Mouser Part Number CRCW060345K3FKEAHP
R25: 590; R_0603_1608Metric_Pad0.98x0.95mm_HandSolder; Mouser Part Number CRCW0603590RFKEA
R26: 2.1k; R_0603_1608Metric_Pad0.98x0.95mm_HandSolder; Mouser Part Number CRCW06032K10FKEA
R27: 402k; R_0603_1608Metric_Pad0.98x0.95mm_HandSolder; Mouser Part Number CRCW0603402KFKEAC
R29: 10k; R_0603_1608Metric_Pad0.98x0.95mm_HandSolder; Mouser Part Number CRCW060310K0FKEI
R30: 8K; R_0603_1608Metric_Pad0.98x0.95mm_HandSolder; Mouser Part Number CRCW060310K0FKEI
R31: 19k; R_0603_1608Metric_Pad0.98x0.95mm_HandSolder

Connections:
+24V: 24V2.1, C45.1, C46.1, IC3.15 (OUT_1), IC3.16 (OUT_2), R29.1; also elsewhere on the board
/24V_Ext: C42.1, C43.1, D17.1 (A1), IC3.1 (IN_1), IC3.2 (IN_2), R24.1; also elsewhere on the board
/Power_Distribution/FAULT: IC3.14 (~FLT), R29.2; also elsewhere on the board
/Power_Distribution/Power Protection/IMON: IC3.10 (IMON), R31.1
/Power_Distribution/Power Protection/MODE: IC3.6 (MODE), R27.1
/Power_Distribution/Power Protection/OVP: IC3.5 (OVP), R25.2, R26.1
/Power_Distribution/Power Protection/RTN: C44.2, IC3.8 (RTN), IC3.17 (EP), R26.2, R27.2, R30.2, R31.2
/Power_Distribution/Power Protection/SHDN: IC3.7 (~SHDN)
/Power_Distribution/Power Protection/UVLO: IC3.3 (UVLO), R24.2, R25.1
GND: C42.2, C43.2, C45.2, C46.2, D17.2 (A2), GND1.1, IC3.9 (GND); also elsewhere on the board
unnamed: C44.1, IC3.12 (DVDT)
unnamed: IC3.11 (ILIM), R30.1

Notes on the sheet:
20.88 ms ramp time
Functional Mode Selection
Set to circuit breaker (latchoff) Use 0 ohm resistor for auto-retry (540ms)
Vin protection
ILim(A) = 12/R(k) 1.5A = 12/8kΩ
Overcurrent Protection
Got rid of current monitoring for an onboard led just leaving it here in case
Under/Overvoltage Protection
RTN!=GND Conecting GND to RTN turns off RPP!
OVP set to 27v for buck max voltage of 28v

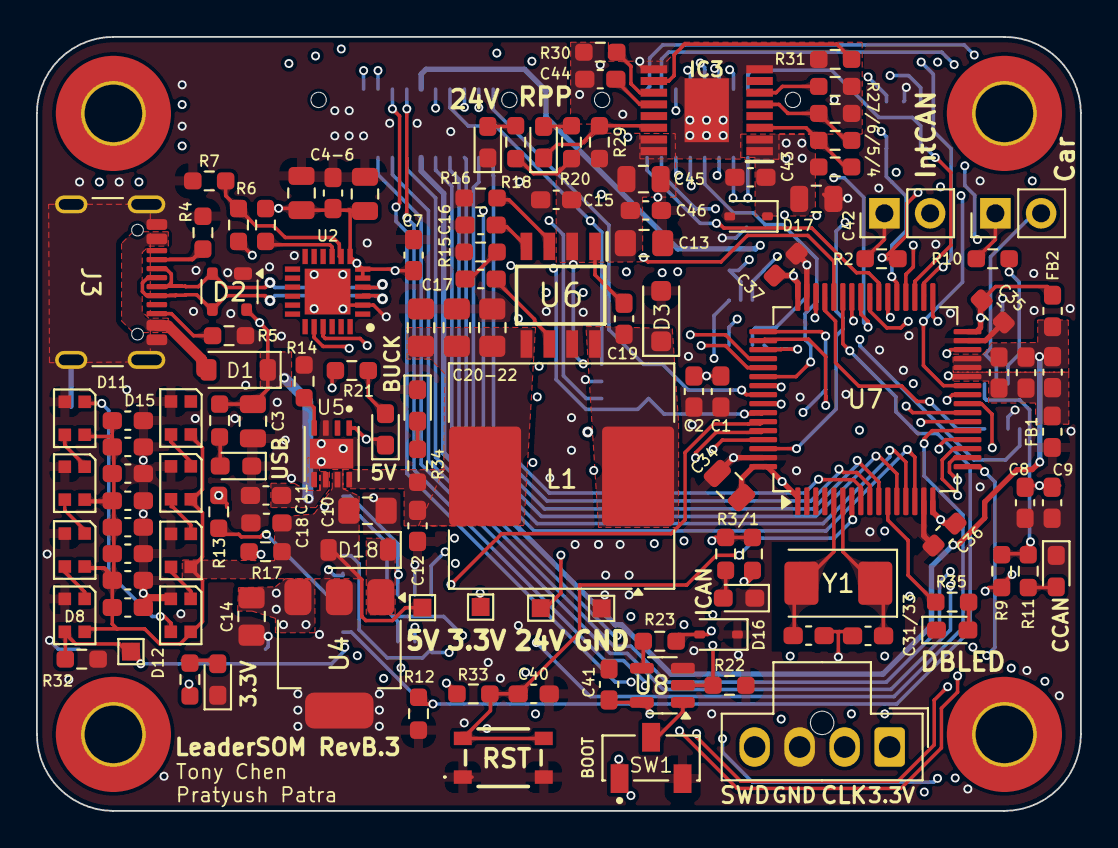
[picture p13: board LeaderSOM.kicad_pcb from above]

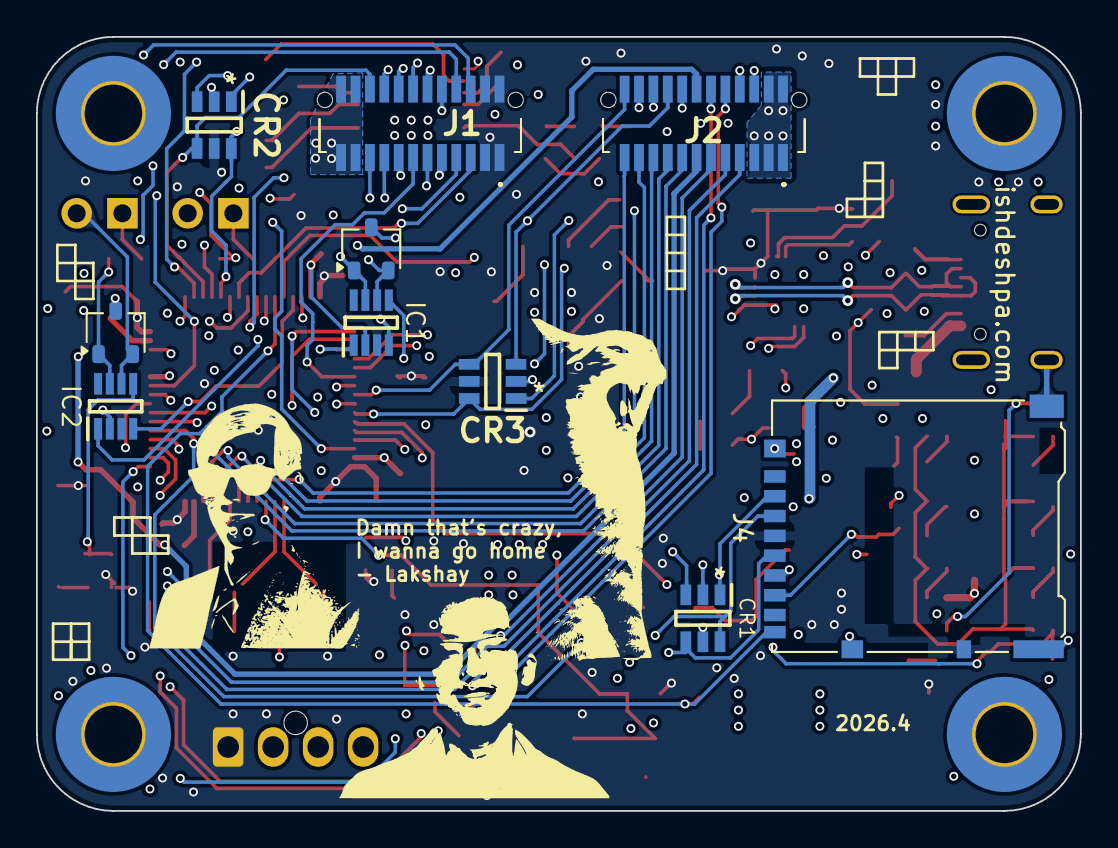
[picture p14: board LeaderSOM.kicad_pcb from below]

Board: 4 copper layers, 58.0 x 43.0 mm, 142 parts (12 on the bottom side), 109 nets.

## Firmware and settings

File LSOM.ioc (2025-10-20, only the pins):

Mcu.UserName=STM32G473RETx
PA11.Signal=FDCAN1_RX
PA12.Signal=FDCAN1_TX
PA13.Signal=SYS_JTMS-SWDIO
PA14.Signal=SYS_JTCK-SWCLK
PA15.Signal=FDCAN3_TX
PA3.Signal=ADC1_IN4
PA4.Signal=SPI1_NSS
PA5.Signal=SPI1_SCK
PA6.Signal=SPI1_MISO
PA7.Signal=SPI1_MOSI
PA8.Signal=FDCAN3_RX
PA9.Signal=ADC5_IN2
PB10.Signal=USART3_TX
PB11.Signal=USART3_RX
PB6.Signal=GPIO_Output
PB7.Signal=GPIO_Input
PB8-BOOT0.Signal=GPIO_Input
PC3.Signal=ADC1_IN9
PF0-OSC_IN.Signal=RCC_OSC_IN
PF1-OSC_OUT.Signal=RCC_OSC_OUT
PG10-NRST.Signal=GPIO_Input

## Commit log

2023-09-23 Updated footprint libraries
2023-11-21 V1.0 (#1) ( no bom )
    * Added subsheets
    * Updated sheets with copies from other boards
    * Updated UART
    * Updated pin assignments
    * Updated pinouts and added protection circuitry for signals
    * Updated power distribution design
    * Updated power filtering
    * Finished power distribution
    * Updated CAN circuitry and used new power protection PMOS
    * Finished CAN circuitry
    * Fixed CAN jumper
    * changed BJT and PMOSFET symbols to standard schematic symbols
    * Added power distribution ferrite bead
    * Updated datasheets
    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
    [CarCAN.kicad_sch, Display.kicad_sch, ExternalCAN.kicad_sch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]
2024-04-27 fix power dist, update to kicad 8
    [CarCAN.kicad_sch, Display.kicad_sch, InternalCAN.kicad_sch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]
2024-10-07 Updated schem for redesign
    [CarCAN.kicad_sch, InternalCAN.kicad_sch, LeaderSOM.kicad_sch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]
2024-10-14 fix lakshay things
    [CarCAN.kicad_sch, LeaderSOM.kicad_sch, SDCard.kicad_sch]
2024-10-16 Updated symbols
    [CarCAN.kicad_sch, Display.kicad_sch, InternalCAN.kicad_sch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]
2024-11-16 laid things out but still need to fix things :(
    [CarCAN.kicad_sch, Display.kicad_sch, InternalCAN.kicad_sch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]
2024-11-18 Cleared up a bunch of constraints violations
    [LeaderSOM.kicad_pcb]
2024-11-20 changed cap on osc
    [LeaderSOM.kicad_pcb, LeaderSOM.kicad_sch, Power_Distribution.kicad_sch]
2024-12-17 fixed can stuff
    [CarCAN.kicad_sch, InternalCAN.kicad_sch, LeaderSOM.kicad_pcb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]
2024-12-17 updated symbol and footprint for lsom
    [LeaderSOM.kicad_pcb]
2025-02-17 added header
    [CarCAN.kicad_sch, LeaderSOM.kicad_pcb]
2025-04-13 hi again lakshay
    [CarCAN.kicad_sch, Display.kicad_sch, InternalCAN.kicad_sch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]
2025-09-06 kicad sharepoint
2025-09-06 starting redesign
    [DYY0016A.stp, Display.kicad_sch, LQFP64-10x10mm.step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]
2025-09-13 MCU pins, PSON power distribution, KiCad-Sharepoint, and 7 seg
    [CarCAN.kicad_sch, Display.kicad_sch, InternalCAN.kicad_sch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]
2025-09-13 net class fixes and ERC
    [CarCAN.kicad_sch, Display.kicad_sch, InternalCAN.kicad_sch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]
2025-09-13 workday for review
    [CarCAN.kicad_sch, Display.kicad_sch, InternalCAN.kicad_sch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]
2025-09-15 i did not pay attention in 316
    [LeaderSOM.kicad_sch, MCU.kicad_sch, Power_Distribution.kicad_sch]
2025-09-17 mcu sheet
    [LeaderSOM.kicad_sch, MCU.kicad_sch, MISC.kicad_sch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]
2025-09-18 macbook hater
    [Display.kicad_sch, MCU.kicad_sch, MISC.kicad_sch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]
2025-09-19 review council
    [CarCAN.kicad_sch, InternalCAN.kicad_sch, LeaderSOM.kicad_sch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]
2025-09-20 review council stuff
    [LeaderSOM.kicad_sch, MCU.kicad_sch, MISC.kicad_sch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]
2025-09-20 just updating symbols
    [LeaderSOM.kicad_sch, MCU.kicad_sch, Power_Distribution.kicad_sch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]
2025-09-20 crazy? i used to be crazy
    [CarCAN.kicad_sch, InternalCAN.kicad_sch, LeaderSOM.kicad_pcb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]
2025-09-23 power layout
    [LeaderSOM.kicad_pcb, Power_Distribution.kicad_sch, Power_Protection.kicad_sch]
2025-09-23 late night premonitions of disaster
    [LeaderSOM.kicad_pcb, MCU.kicad_sch, Power_Distribution.kicad_sch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]
2025-09-23 impending doom is approaching
    [LeaderSOM.kicad_pcb, LeaderSOM.kicad_sch, MCU.kicad_sch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]
2025-09-23 routing nightmare
    [LeaderSOM.kicad_pcb]
2025-09-24 gm meeting sucked cuz it was in belmont
    [LeaderSOM.kicad_pcb, MCU.kicad_sch, Power_Protection.kicad_sch]
2025-09-24 redid the traces
    [LeaderSOM.kicad_pcb, LeaderSOM.kicad_sch, MCU.kicad_sch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]
2025-09-25 ripping my hair out
    [LeaderSOM.kicad_pcb, LeaderSOM.kicad_sch, MCU.kicad_sch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]
2025-09-27 6:21:27 split
    [LeaderSOM.kicad_sch, MCU.kicad_sch, Power_Distribution.kicad_sch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]
2025-10-04 lock in
    [LeaderSOM.kicad_sch, MCU.kicad_sch, Power_Distribution.kicad_sch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]
2025-10-10 fixed LSOM symbol
    [LeaderSOM.kicad_sch, MCU.kicad_sch]
2025-10-11 changing IOC file to only display the internal pins
    [MCU.kicad_sch, Power_Distribution.kicad_sch, Power_Protection.kicad_sch]
2025-10-11 lakshay changes and ioc file was changed
    [MCU.kicad_sch, Power_Distribution.kicad_sch, Power_Protection.kicad_sch]
2025-10-11 JLCPCB BOM and gerbers
    [LeaderSOM-CuBottom.gbr, LeaderSOM-CuIn1.gbr, LeaderSOM-CuIn2.gbr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]
2025-12-01 soldering stuff
2025-12-06 revB for assembly stuff
    [LeaderSOM.kicad_pcb, LeaderSOM.kicad_sch, MCU.kicad_sch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]
2025-12-08 JLCPCB BOM/CPL/Gerbers
    [BOM-LeaderSOM.csv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]
2026-01-18 the emptiness machine - linkin park
    [CarCAN.kicad_sch, LeaderSOM.kicad_pcb, LeaderSOM.kicad_sch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]
2026-03-12 qol changes
    [LeaderSOM.kicad_pcb, MISC.kicad_sch, Power_Distribution.kicad_sch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]
2026-04-27 comp spares with fixed ldo diode
    [BOM-LeaderSOM.csv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]
2026-05-17 added revb.3 changelog
    [LeaderSOM.kicad_sch]
